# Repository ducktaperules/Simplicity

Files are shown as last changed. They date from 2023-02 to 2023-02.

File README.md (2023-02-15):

<h1 align="center">Simplicity</h3>

<p align="center"> A compact and easy to build printed printer
    <br> 
</p>

<p align="center">
  <a href="" rel="noopener">
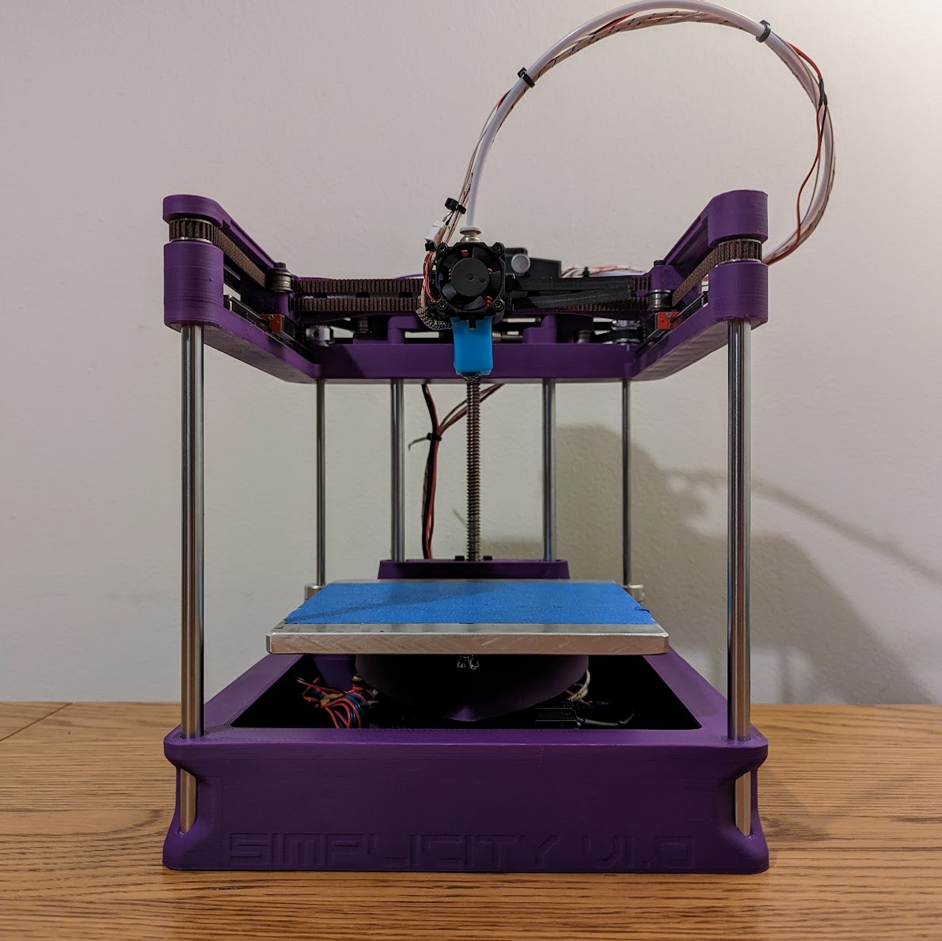
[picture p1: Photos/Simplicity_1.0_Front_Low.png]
Project logo
 </a>
</p>

  <br>

<!-- 
## 📝 Jump To Useful Things:
- [Quick Start](#get_started)
- [Info about Simplicity](#info)
- [Features](#features)
- [Inspiration](#inspiration)
- [Ethos](#ethos)
- [To Do List](#to_do_list)
- [Future Scope](#future_scope)
- [Authors](#authors)
- [Acknowledgments](#acknowledgments)
-->

## 👏 Quick Start
### - [BOM And CAD](/CAD/)
### - [Build Guide](/Instructions/)

  <br>

## 🧐 Info about Simplicity 
Simplicity was designed as a compact desktop printer for the everyman. Its well suited to printing small parts quickly and accurately. Its easy to source, build and maintain, whilst looking good enough that you can keep it on show and accessible at all times.

## 📱 Features 
 - CoreXY Design
 - 3D Printed Frame (prints on 220x220mm bed)
 - 120x120x100mm print volume (easy to extend Z as needed)
 - Voron V0 Bed Support
 - Looks Good
 - Few separate parts to print.
 - Less than 500g of filament to print all parts.
 - Integrated belt tension adjustment.
 - Bottom mounted motors for improved stability

<br>

## 💡 Inspiration 
### Voron V0 (https://github.com/VoronDesign/Voron-0)
The V0 is one of the most popular desktop printers that has shown what small format FDM printers are capable of. I wanted one for a long time however theres 3 main things that have put me off:
 -  Sourcing - There are so many the different parts to source. Aluminum extrusions, Odd size motors, Custom Beds, Specific extruders, acrylic panels, 
 - Printing - As of today the V0.2 print list currently has 143 parts to print. The thought of having to download, organize, slice, print and clean this many parts is a daunting task in its self. Especially if you don't already own a printer that tuned to perfection.
- Building - For some this is the fun bit, but for many this can be a tedious and frustrating endeavour. 

### Rolohaun Rook (https://github.com/rolohaun/Rook)
The Rook is a relatively new printer focused around making small format printers more accessible. I think the idea of using a printed frame is great and theres now enough of them out in the wild to prove that this can be a reliable option if designed well. I also love the use of vertical linear rods for both the bed and as structural frame component. 

That said, the Rook design optimized for function over aesthetics. IMO it also has an unnecessary number of individual parts to print that require a decent tolerance to work correctly. 

<br>

## 🤘 Ethos 

### Simple to Print
Simplicity is designed to have as few separate parts as possible, all of which should be printable without supports. Its also designed so that tolerances in most places are not critical and everything should fit together first try.

### Built from common parts
Due to the small lightweight design, good results can easily be achieved with cheap components or old spare parts. Any Junker 42mm stepper motors will give speeds and accelerations. Im also using the Creality hot end as they are available everywhere and many even have them spare from previous printers.

### Easy to mod
The stock configuration i have provided is the minimum needed to get up and running however i expect there will be many mods allowing better cooling, different print heads, enclosures, and electronics mounting for many different control boards. 
<br>The full .STEP file is now available for modding in the CAD folder.

<br>

## 📋 To Do List 
There are a few things i need to do in the short term.
 - Upload STL files ✅
 - Upload STEP files
 - Add pictures ✅
 - Add instruction manual ✅
 - Write BOM ✅(kinda)
 - SORT OUT LICENSE
 - Design parts variant that use M3 heat set inserts rather than self tapping screws.
 - Maybe Belted Z Mod

<br>

## 🚀 Future Scope 
There are a lot of things i would like to improve in the future.
 - Printhead with built in part cooling fans 
 - Electronics Cover for those who want to  hide their shame
 - Full enclosure with door and lid for better printing of ABS

<br>

## ✍️ Authors 
- [@ducktaperules](https://github.com/ducktaperules) - Idea & Initial work

<br>

## 🎉 Acknowledgments 
- [@rolohaun](https://github.com/rolohaun) - Thanks for the inspiration and for hosting a great community on discord who provide constant motivation.

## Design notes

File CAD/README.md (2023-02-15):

<p align="center">
  <a href="" rel="noopener">
 
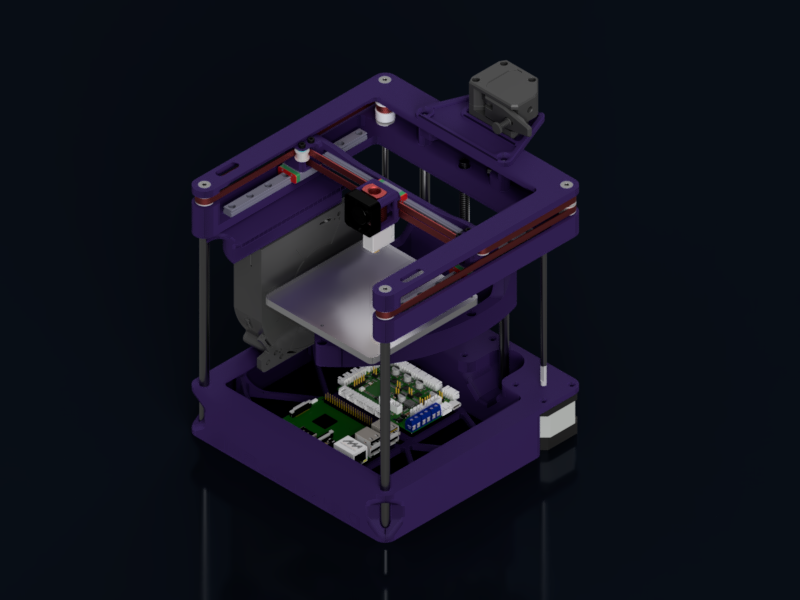
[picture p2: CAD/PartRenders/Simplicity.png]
</a>
</p>

<h1 align="center">Parts List</h1>

## BOM

Big Parts:
 - Control Board - I recommend SKR Pico with raspberry pi and klipper, but you can use whatever printer board you have access to.
 - 3x NEMA 17 stepper motors less than 40mm in length (For XYZ axis).
 - Extruder and Stepper - Any you have available. The stock Creality will fit but i recommend a dual gear like the bondtech BMG clones available from ali-express or amazon.
 - Hot End - Again, creality ender/CR10 hot end is fine but i recommend a high flow nozzle. im using a cheep volcano block and nozzle from amazon.
 - Bed - 120x120mm beds compatible with Voron V0 or Rook should fit. Otherwise Im using a diy bed made from a 150x150mm scrap of aluminum with V0 compatible mounting. If not using a printed bed i have seen some Rook's with printed beds. 
 - Power supply - whatever you can find 24V PSU is ideal but im just using a 20V 6.5A Dell laptop supply, its a little less powerfull but much easier to mount externally.
 - 3010 fan for hot end.
 - Optional 120mm radial blower for part cooling.

Bearings & Drive:
 - 3x 150mm MGN9 rails with MGN9C carriages
 - 4x 8mm smooth rods 200mm length.
 - 2x LM8UU Long 45mm bearings (dual short bearings might work instead but not tested)
 - 1x 8mm lead screw and nut, ~150mm length
 - 20x F695 Bearings (5x13x4 flanged). Usually available in sets of 10.
 - 8x F623 Bearings (3x10x4 flanged). Usually available in sets of 10.
 - 2x 20T GT2 pulleys.
 - 2m of Gates GT2 Belt
 - 2x 5mm to 5mm motor couplers
 - 1x 5mm to 8mm motor coupler 
 - 2x 160mm 5mm rod (steel, aluminum, carbon, shouldn't matter what)

Hardware: 
 - 24 M2.5 x 8mm self tapping screws (i used Torx T10, will try find a good link ASAP)
 - 6 M2.5 x 16mm self tapping screws (i used Torx T10, will try find a good link ASAP)
 - 6x M5x30 CSK
 - 2x M5x25 CSK (+4 if using my electronics tray)
 - 2x M5x25 Cap Head (tension adjusters so cap or dome works too)
 - 8x M5 Heatset Inserts (7mm diameter by <8mm deep ),(+4 if using my electronics tray)
 - 20x M5 Washer (should be 1mm thick)
 - 8x M3 Washer (should be 0.5mm thick)
 - 8x M3x25 Cap Head (or dome head if your a sadist)
 - 4x M3x6 Cap Head (see above)
 - 12x M3x8 CSK (for stepper motors)

---

## Printed Partrs

I have been printing all parts in ABS+ as i plan to print PETG in the future, but if you only plan to print PLA i would expect a PLA frame to be fine.

I sliced with 0.2mm layers, 15% infill, 3 perimiters and 4/5 bottom/top layers.

Total filament used was around 430g and total print time was around 24 hours on my ender 5 plus with conservative speed settings.

### Frame Base
The base is the largest part. it should print top side down.
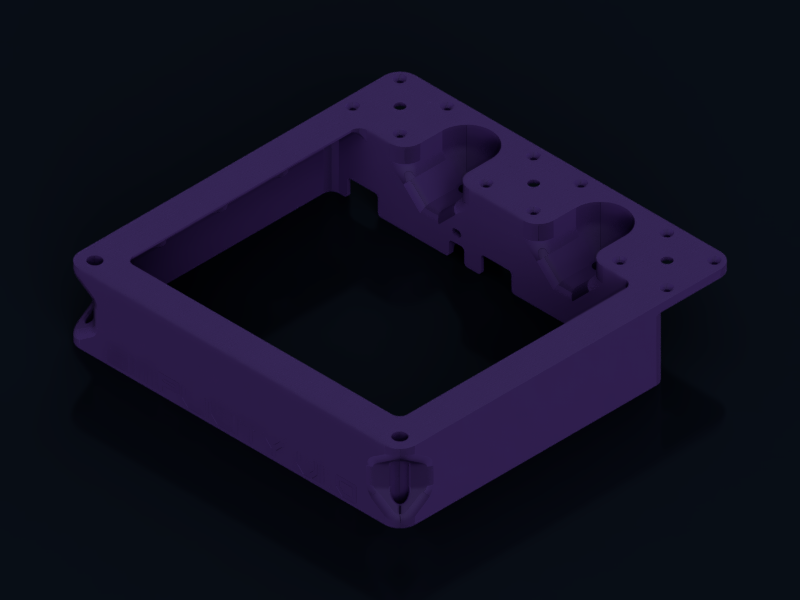
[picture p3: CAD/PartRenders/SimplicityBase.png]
<p></a></p>

### Frame Mid and Frame Top
These 2 parts bolt together to form the main top assembly.
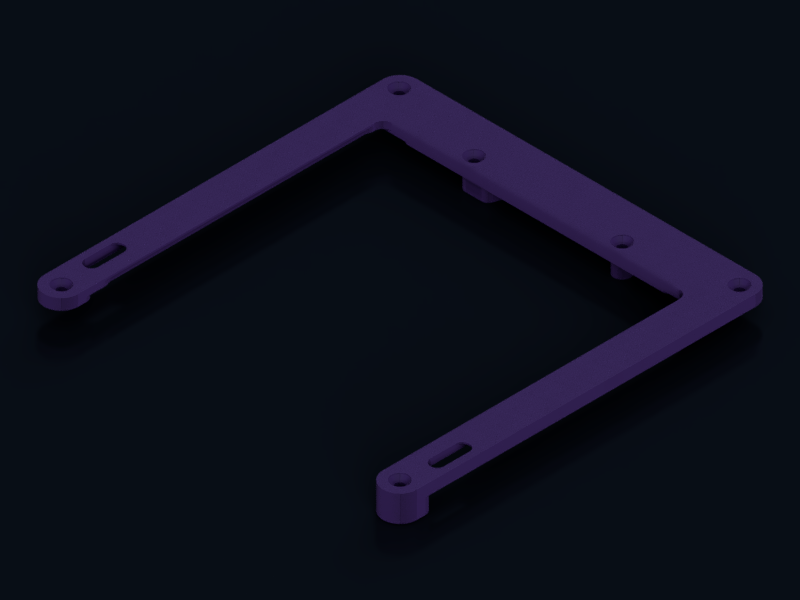
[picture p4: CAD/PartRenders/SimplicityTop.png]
<p></a>
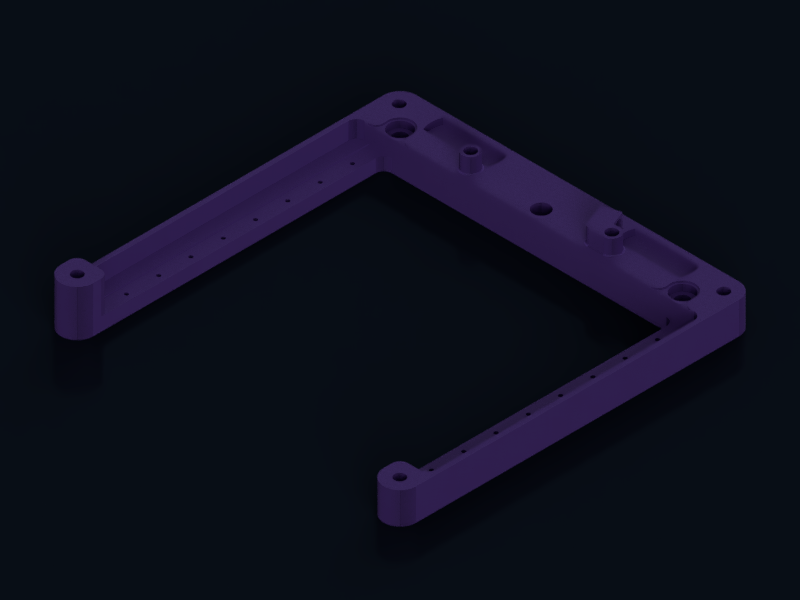
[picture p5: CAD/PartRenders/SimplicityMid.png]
</a></p>

### Tensioner (x2)
You need 2 of these. They hold the adjustable belt pulleys to tension the belt. They should sit flat on the bed with the widest part of the slope at the bottom. 
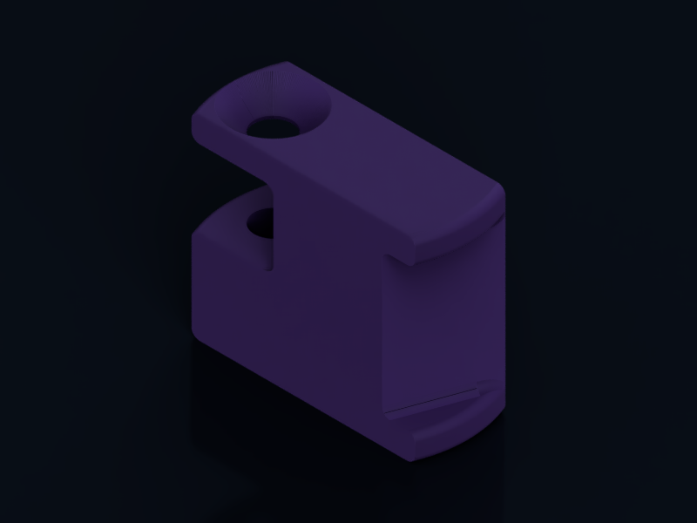
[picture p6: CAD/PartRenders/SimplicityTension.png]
<p></a></p>

### X Gantry
Printed on its back with the rail surface on the top.
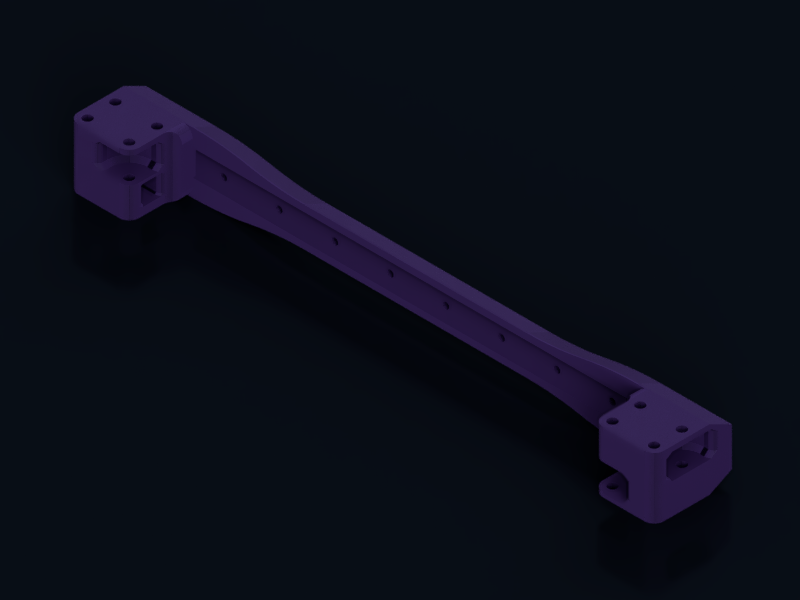
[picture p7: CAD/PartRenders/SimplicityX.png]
<p></a></p>

### Print Head
Printed on its back.
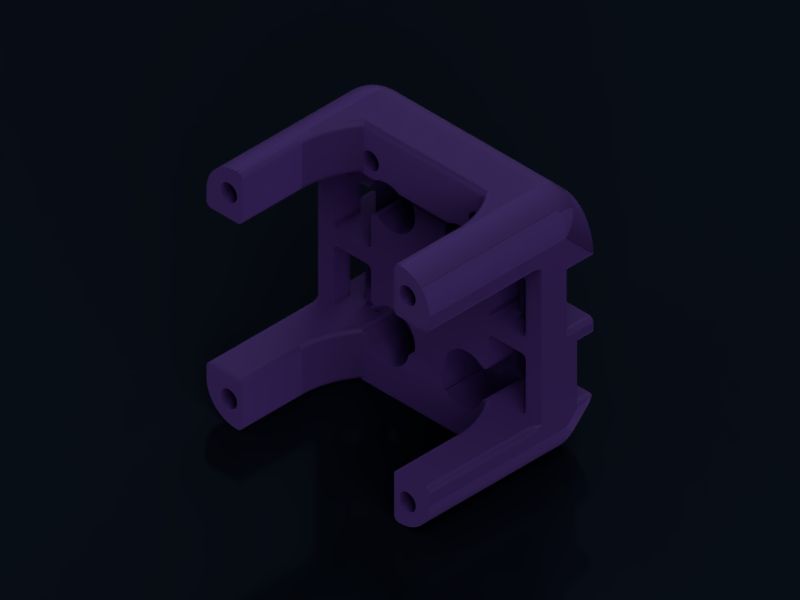
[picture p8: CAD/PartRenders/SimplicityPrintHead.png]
<p></a></p>

### Bed
Printed with the large flat side down, a small amount of support is usually needed for the overhand near the nut for the threaded rod
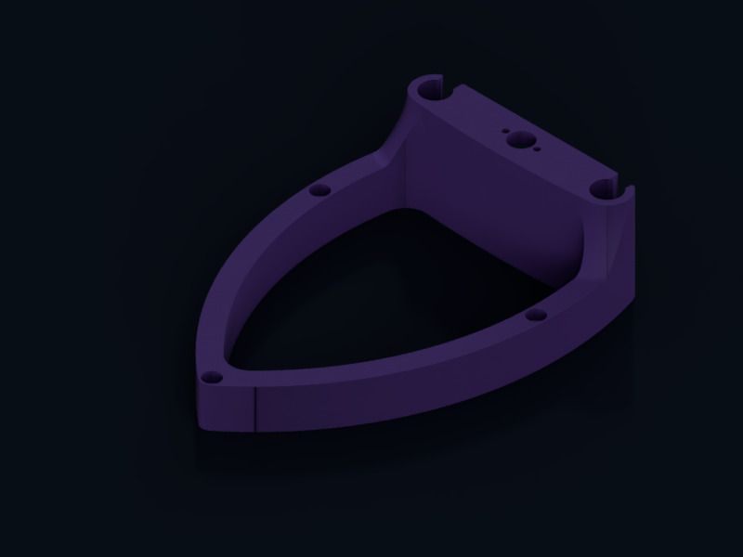
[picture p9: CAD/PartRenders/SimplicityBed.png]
<p></a></p>

### Extruder mount
Optional part that will alow for easy mounting of most extruders that use a standard stepper motor. I have used both the original Creality extruder as well as the bondtech Clone shown in my photos.
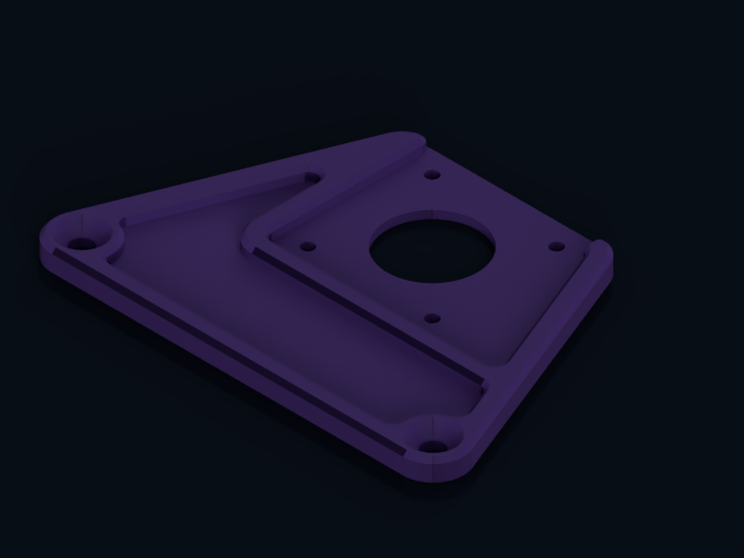
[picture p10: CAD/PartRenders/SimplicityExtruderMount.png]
<p></a></p>

### Electronics mount
Optional part that will alow for easy mounting of raspberry Pi and SKR Pico driver board. if your using something else this part can be modified to support different control boards.
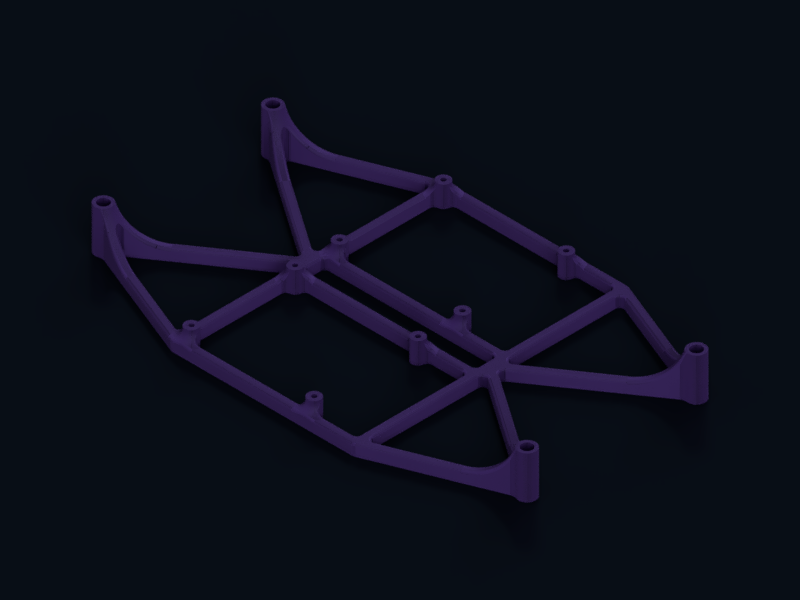
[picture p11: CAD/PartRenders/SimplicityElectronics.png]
<p></a></p>

### Cooling
This is a quick bodge to add an RCS style part cooling fan. its not optimized but it will get you going. it takes a 120mm blower fan. It fits mine, I dont know if they are all the same or not.
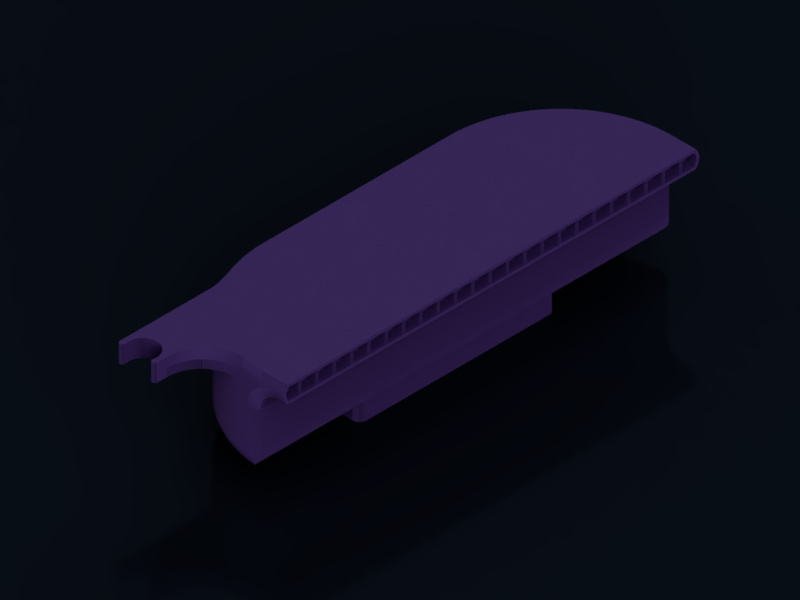
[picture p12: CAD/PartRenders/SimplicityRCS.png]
<p></a>
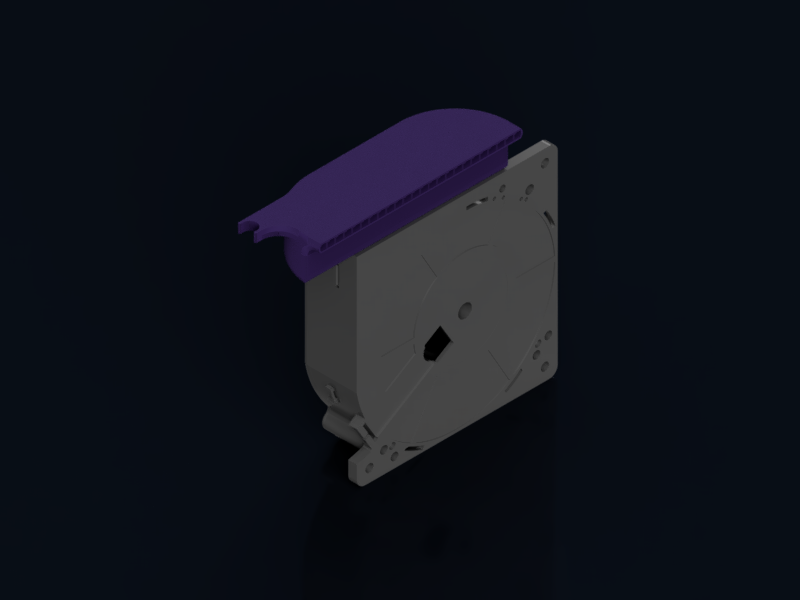
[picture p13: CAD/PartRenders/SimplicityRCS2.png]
</a></p>

### Draft Shield (Guard)
CURRENTLY UNTESTED - This is a simple print that can be printed in vase mode and is designed to provide a semi inclosed bed, offering a little protection from drafts. Its not compatible with the cooling fan above
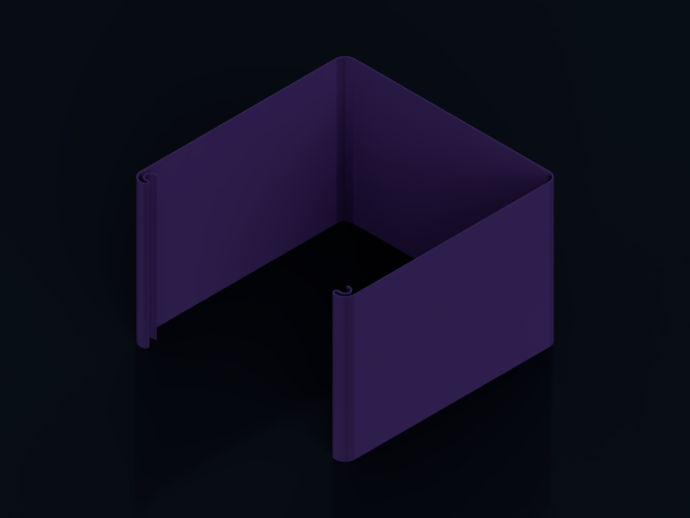
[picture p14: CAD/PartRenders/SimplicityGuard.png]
<p></a></p>

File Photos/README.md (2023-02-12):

<h1 align="center">Gallery</h1>

</a>
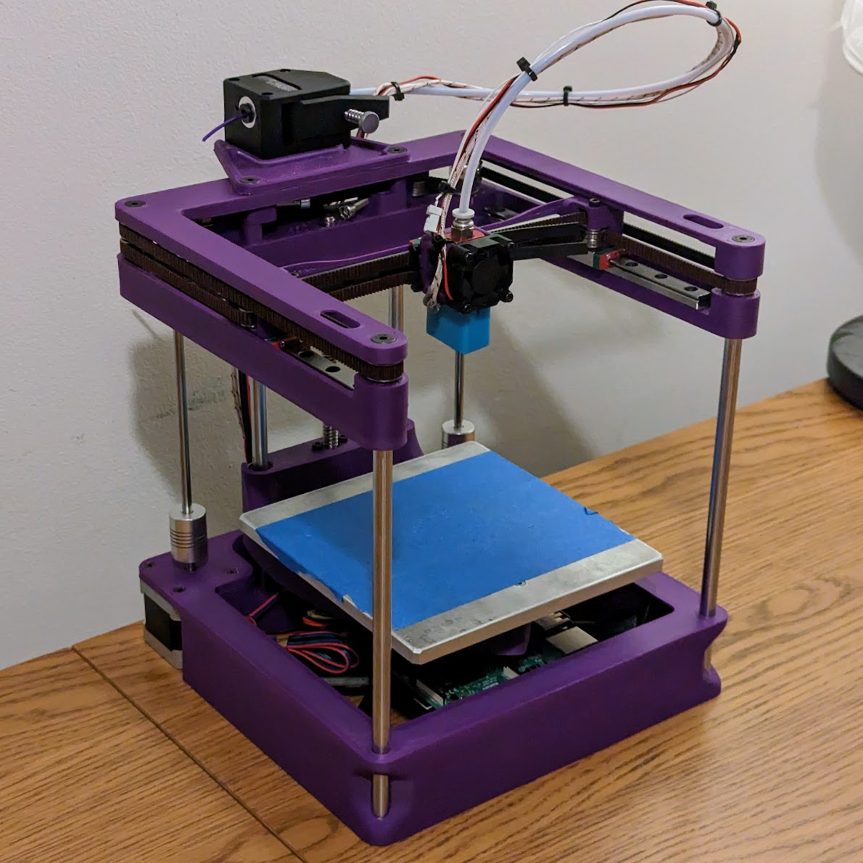
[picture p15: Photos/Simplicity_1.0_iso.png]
</a>
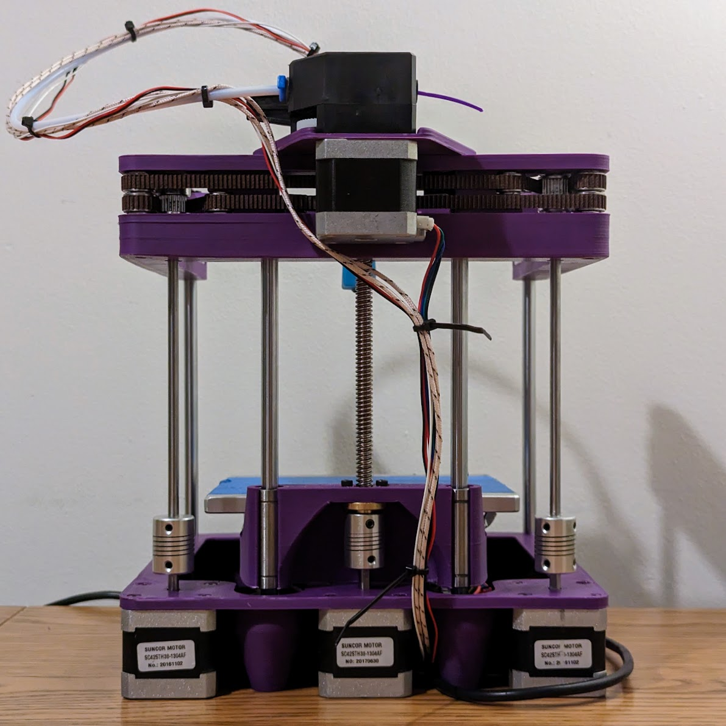
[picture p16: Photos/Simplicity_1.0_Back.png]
</a>
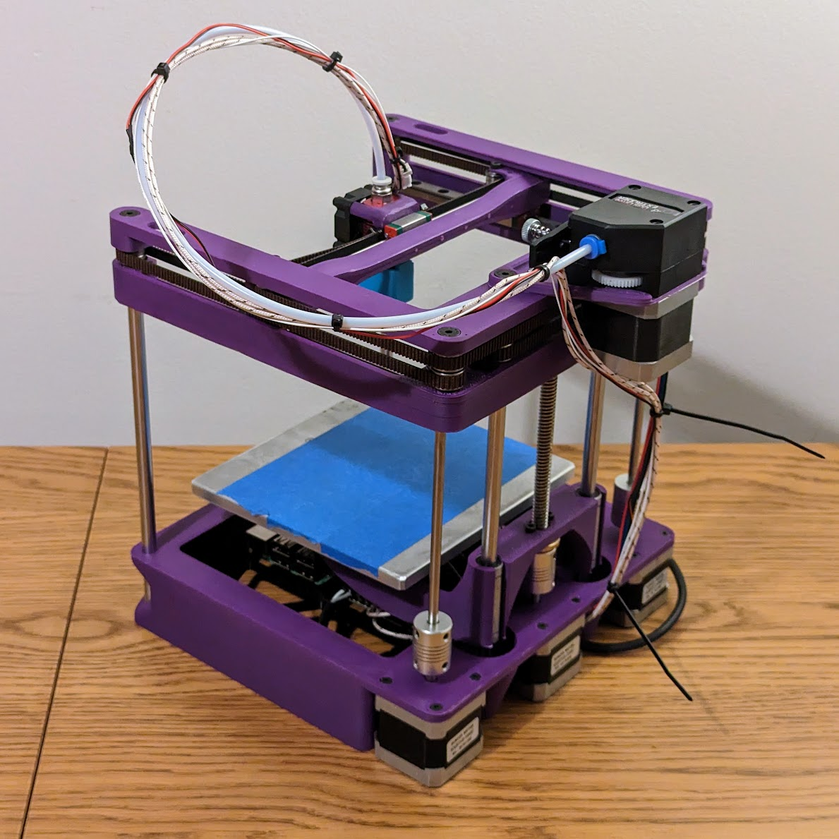
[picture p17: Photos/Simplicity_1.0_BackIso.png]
</a>
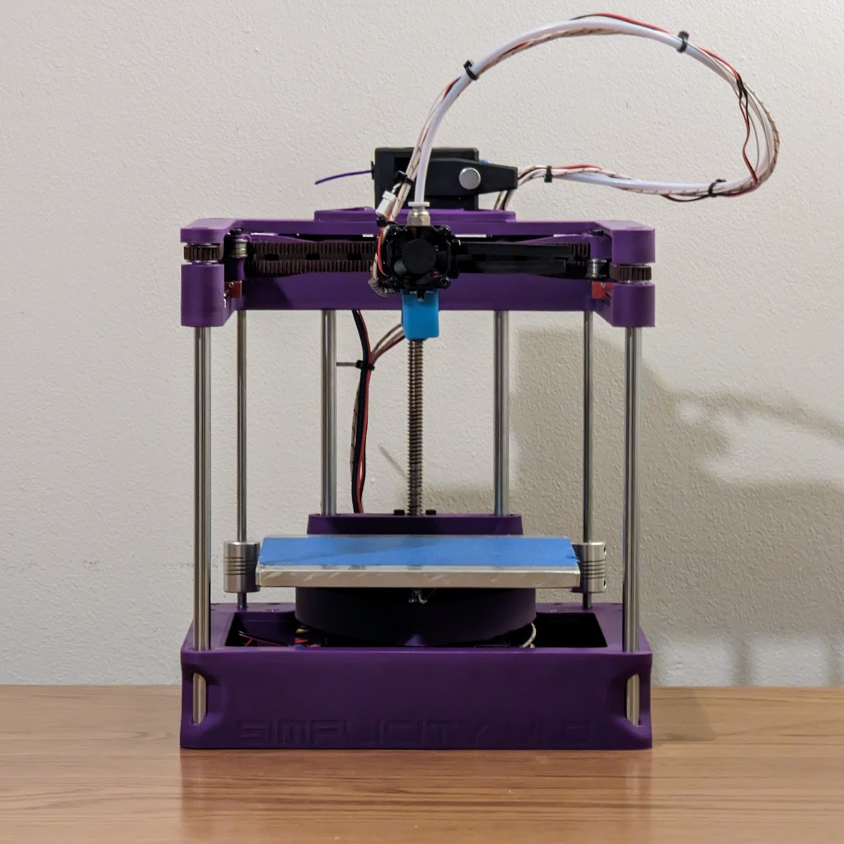
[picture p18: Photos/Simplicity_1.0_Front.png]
</a>

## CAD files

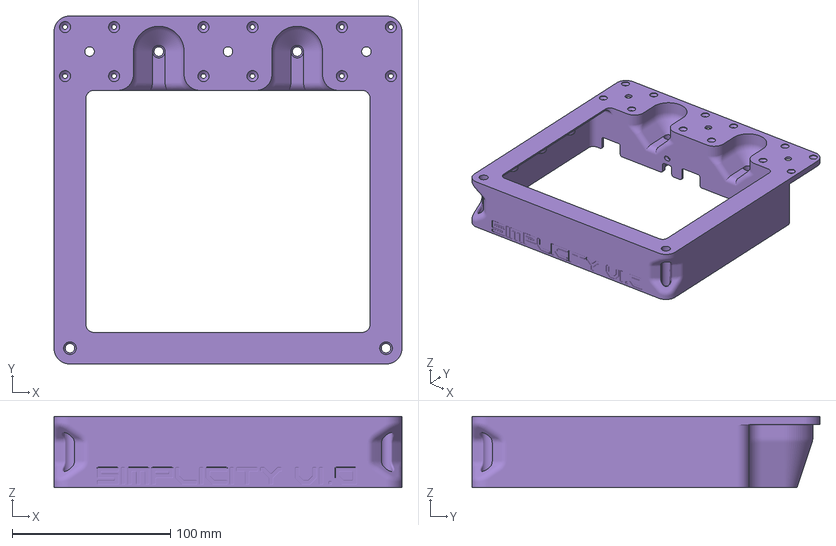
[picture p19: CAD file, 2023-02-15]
CAD/PartFiles/SimplicityBase.3mf
220.0 x 220.0 x 45.0 mm

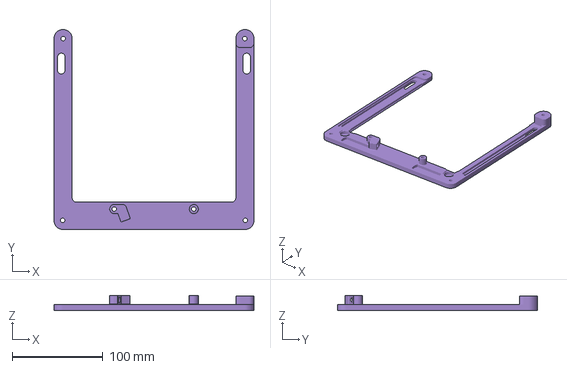
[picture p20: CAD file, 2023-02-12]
CAD/PartFiles/SimplicityTop.3mf
220.0 x 220.0 x 16.0 mm

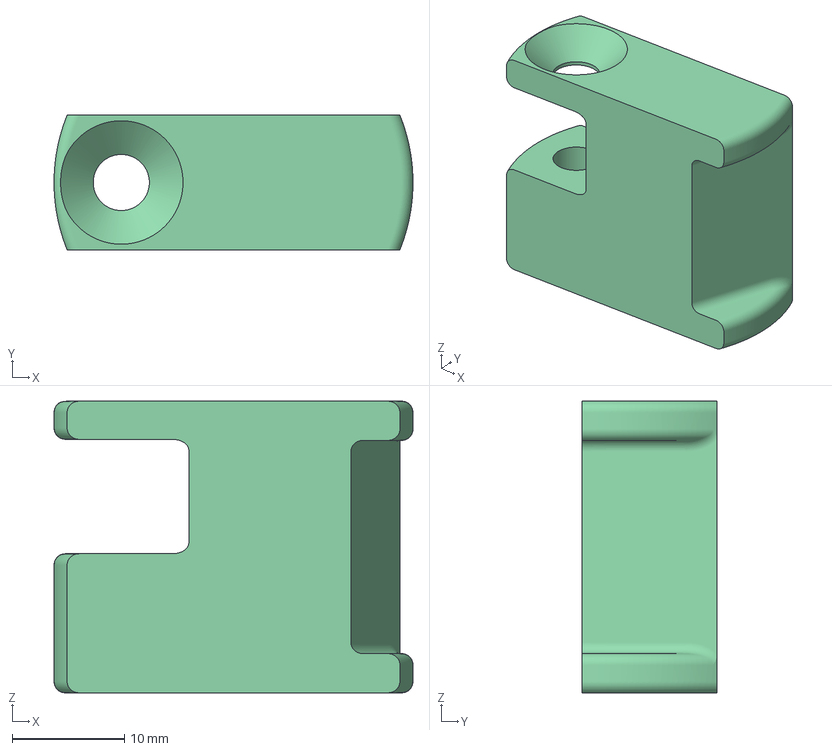
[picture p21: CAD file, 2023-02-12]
CAD/PartFiles/SimplicityTension.3mf
32.0 x 12.0 x 26.0 mm

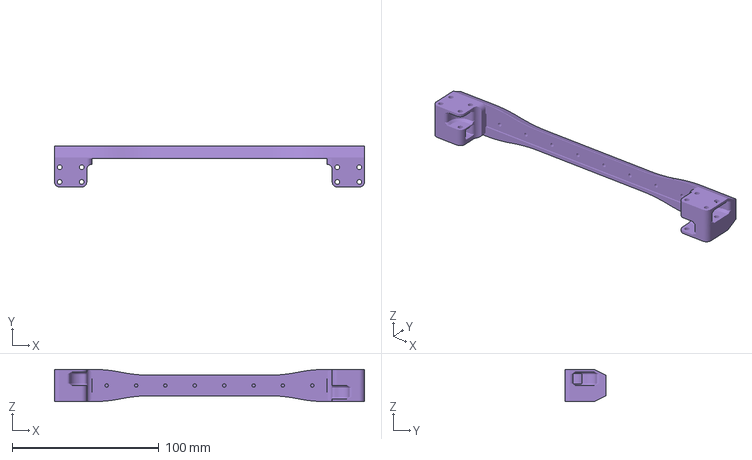
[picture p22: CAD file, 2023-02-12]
CAD/PartFiles/SimplicityX.3mf
211.0 x 28.0 x 22.0 mm

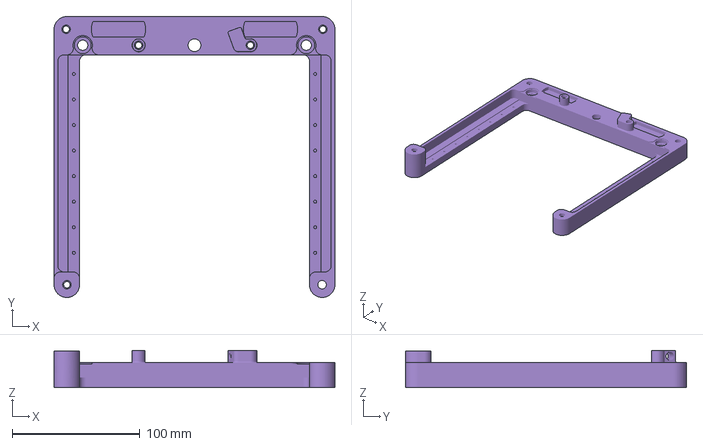
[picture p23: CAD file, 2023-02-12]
CAD/PartFiles/SimplicityMid.3mf
220.0 x 220.0 x 29.0 mm

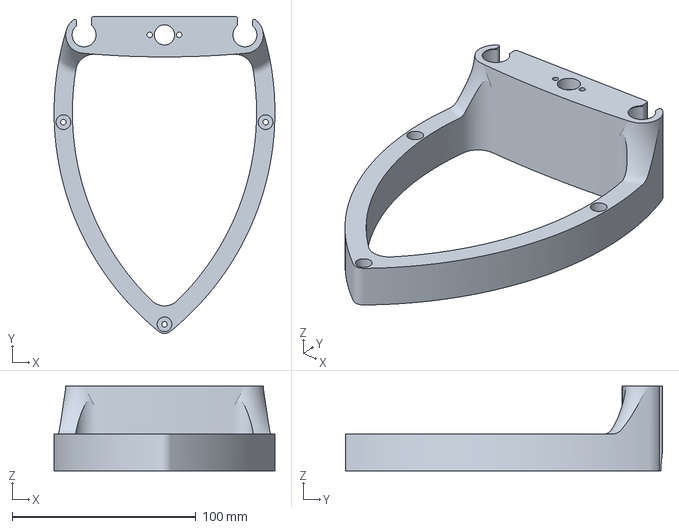
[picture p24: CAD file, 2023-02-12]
CAD/PartFiles/SimplicityBed.3mf
120.2 x 172.5 x 46.0 mm

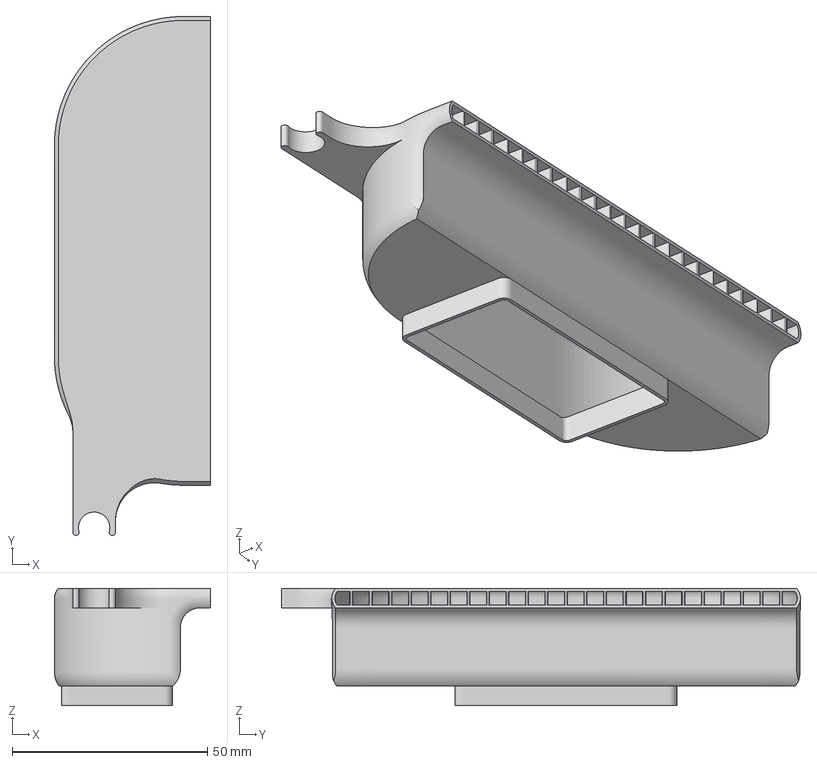
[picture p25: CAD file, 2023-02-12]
CAD/PartFiles/SimplicityRCS.3mf
40.0 x 132.8 x 30.0 mm

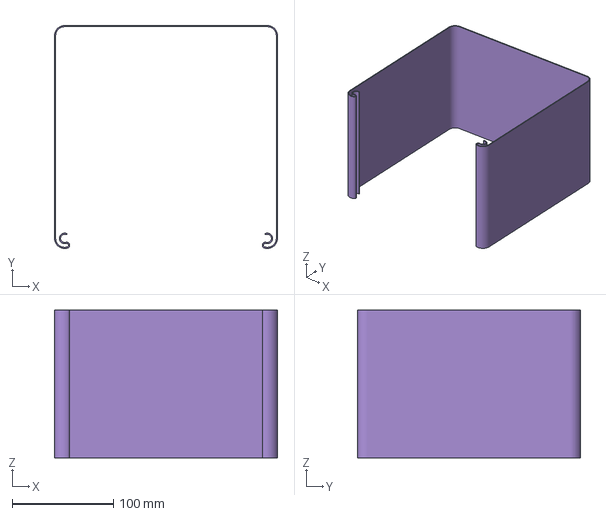
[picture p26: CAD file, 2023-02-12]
CAD/PartFiles/SimplicityGuard.3mf
220.0 x 220.0 x 146.0 mm

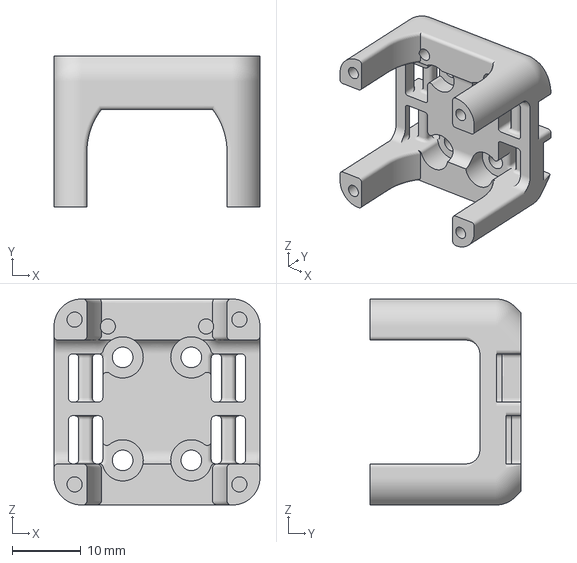
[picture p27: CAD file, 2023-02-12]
CAD/PartFiles/SimplicityPrintHead.3mf
30.0 x 22.0 x 30.0 mm

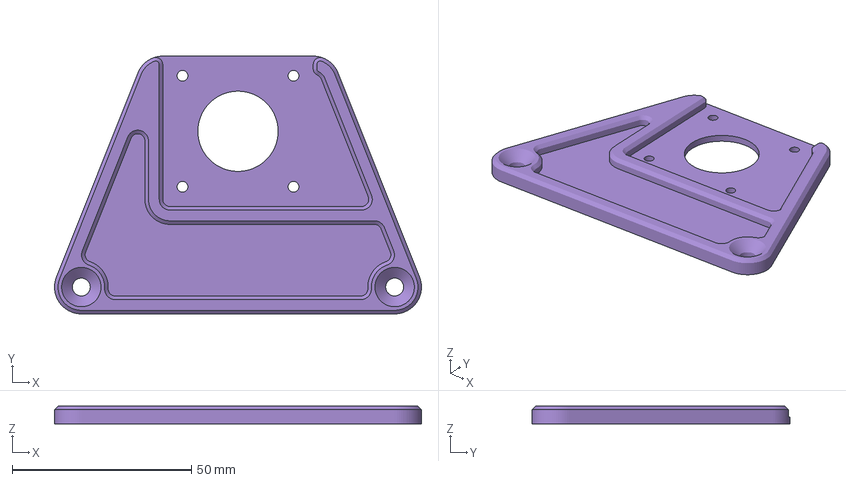
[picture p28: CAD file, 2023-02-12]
CAD/PartFiles/SimplicityExtruderMount.3mf
102.5 x 72.0 x 5.00 mm

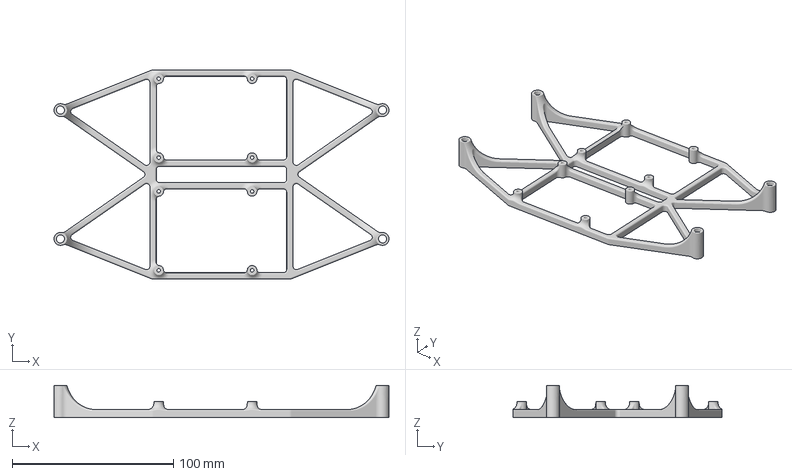
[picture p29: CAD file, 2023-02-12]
CAD/PartFiles/SimplicityElectronics.3mf
208.0 x 130.0 x 20.0 mm

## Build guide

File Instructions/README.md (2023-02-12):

<h1 align="center">Build Guide</h1>

## Step 1 - print and prep your parts

Print all nessacary parts from the part list found in the [parts list here](/CAD/)
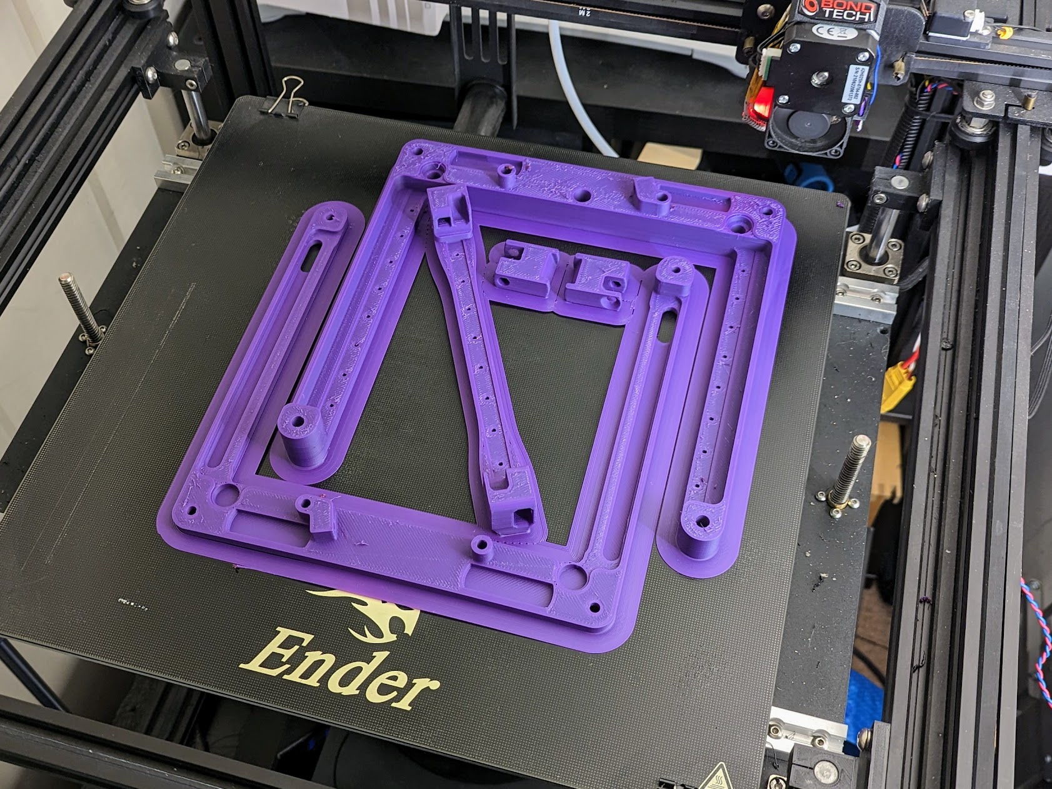
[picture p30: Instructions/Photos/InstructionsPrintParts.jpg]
<p></a></p>

Remove any brims and support. deburr any sharp edegs and remove any bumps on surfaces.
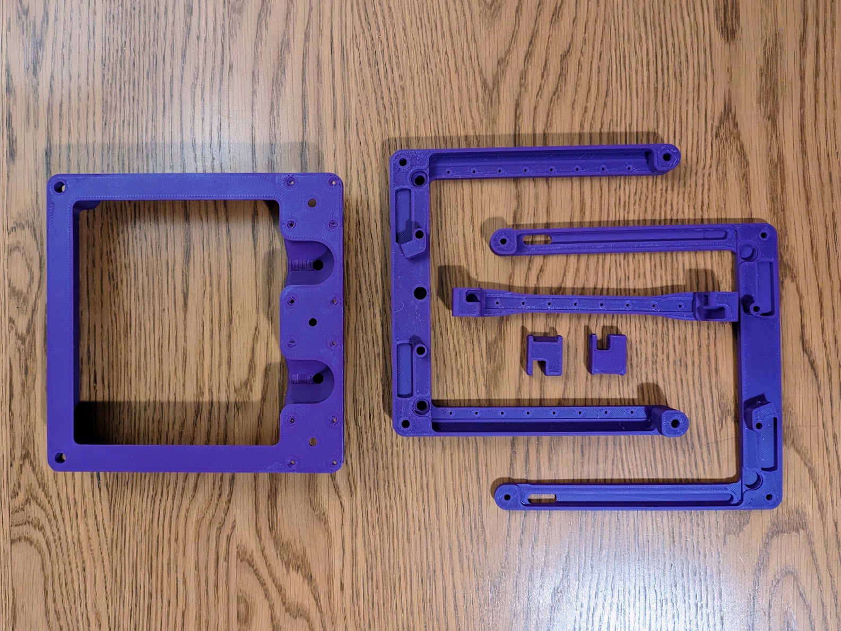
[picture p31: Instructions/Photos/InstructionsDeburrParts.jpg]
<p></a></p>

I recommend to clearance drill most holes to the correct size to ensure easy assembly.

drill 3mm for the 8 holes in the X stage, the 12 stepper motor screws in the base part, the 4 in the Print Head, and the 5 in the bed mount.
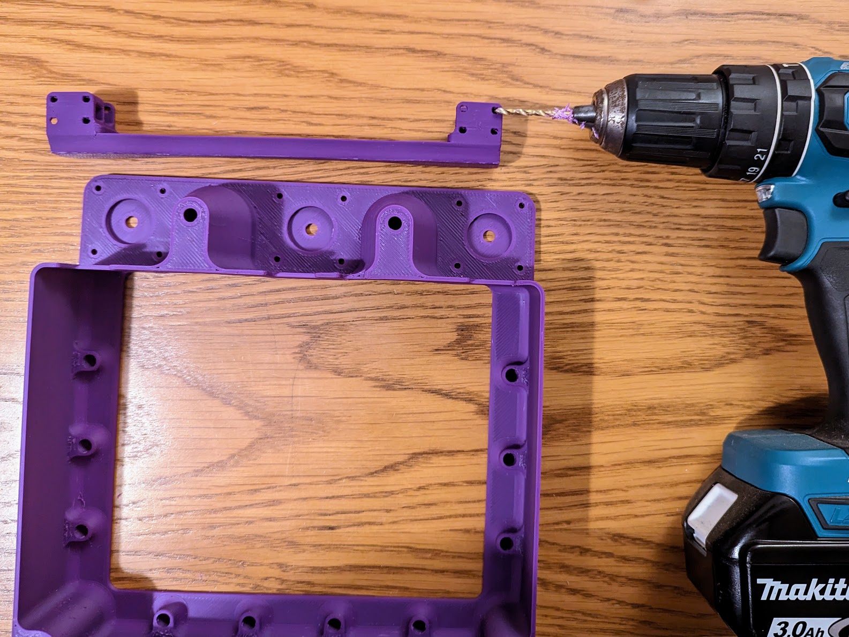
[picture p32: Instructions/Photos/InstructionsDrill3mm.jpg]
<p></a></p>

drill 5mm for the 7 holes in both the mid and top parts (dont forget the sideways one for the tensioner), as well as the holes through the tensioners and the 2 in the extruder mount if your using it.
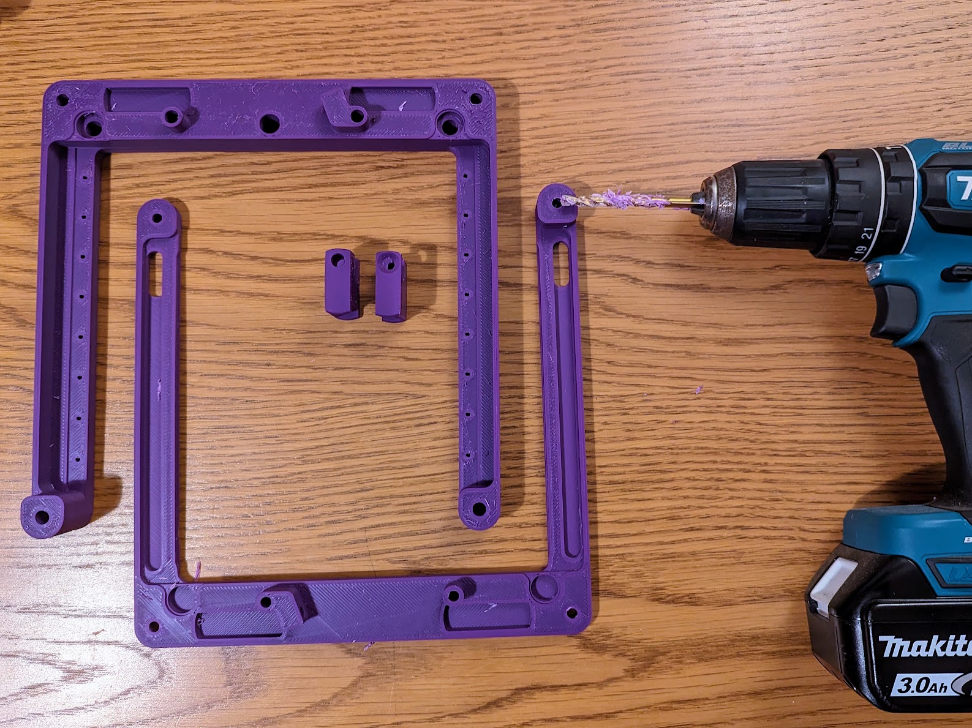
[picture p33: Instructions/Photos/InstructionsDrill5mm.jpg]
<p></a></p>

drill 8mm for the 2 holes in both the base and mid parts.

IMPORTANT NOTE: These 8mm holes do not go all the way through so drill carefully till you touch the step. On the base this is most the way through, on the mid part its about 15mm in.
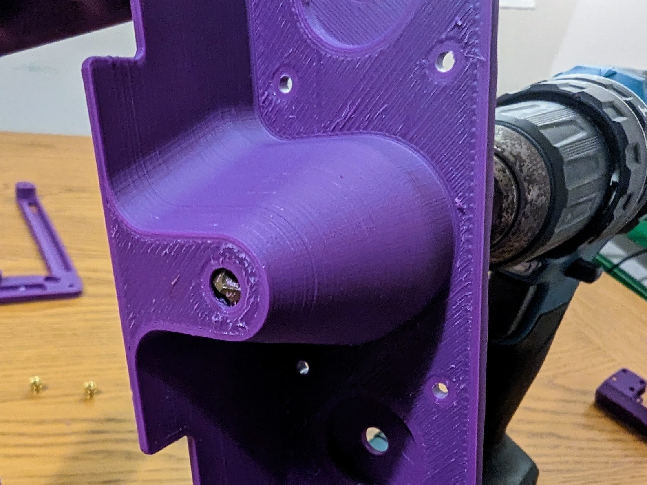
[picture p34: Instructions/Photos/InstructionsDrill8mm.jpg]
<p></a>
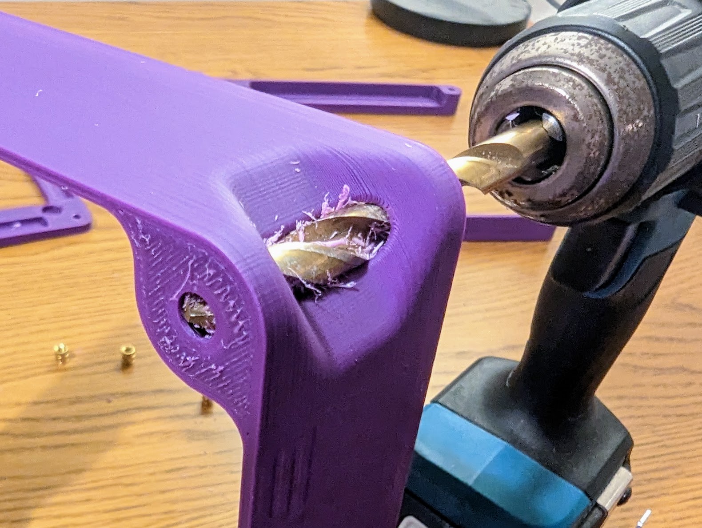
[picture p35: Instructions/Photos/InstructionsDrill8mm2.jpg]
</a></p>

Finally put the M5 heat set inserts in. There are 7 in the mid part, 1 in the top and 1 in each tensioner.
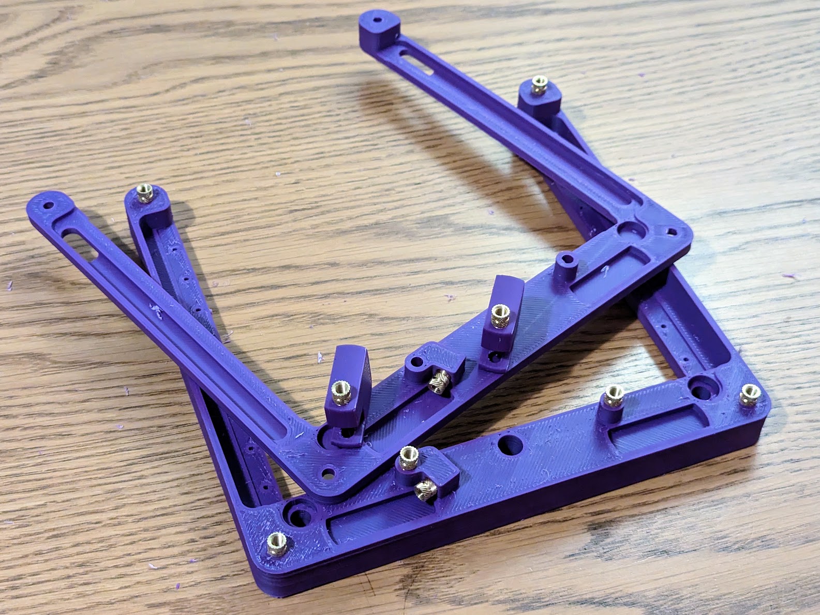
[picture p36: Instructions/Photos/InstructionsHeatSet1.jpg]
<p></a>
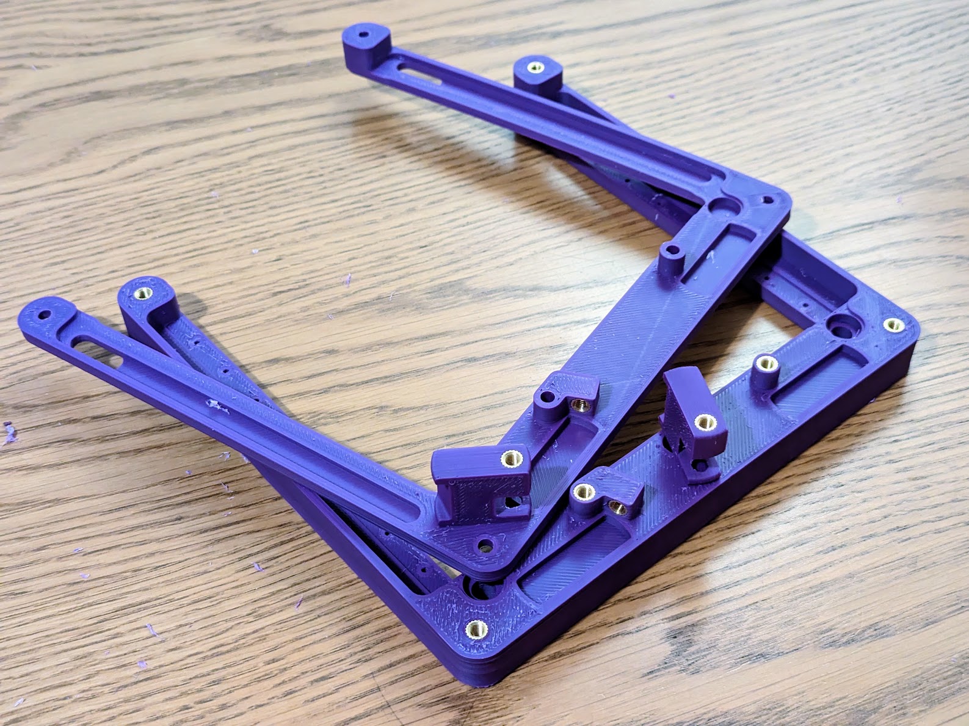
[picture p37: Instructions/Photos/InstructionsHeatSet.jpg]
</a></p>

---

## Step 2 - Build The Base

The 8mm Steel rods can be inserted into the 4 holes in the base. they must be pushed down until they bottom out on the lip at the bottom of the print
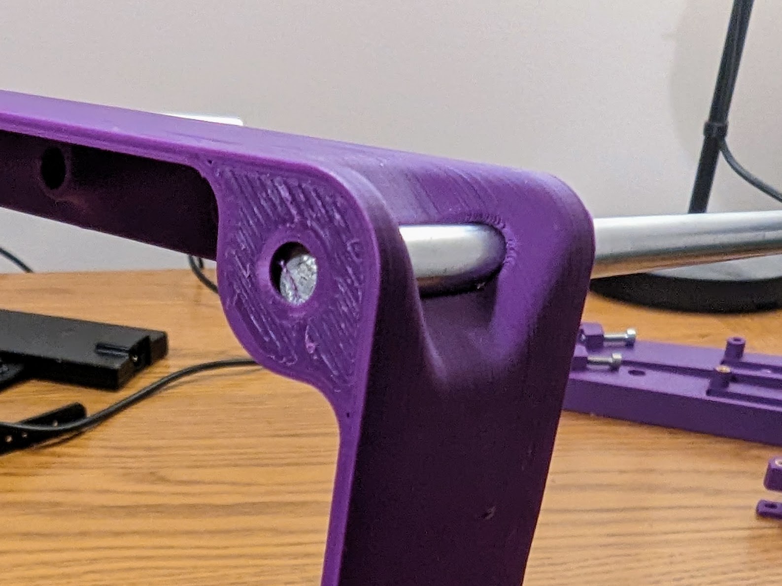
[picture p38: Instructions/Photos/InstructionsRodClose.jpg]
<p></a></p>

Next the 3 drive steppers can be mounted at the back with 12x M3x8 CSK screws. their cables or plugs should face inwards towards the electronics.
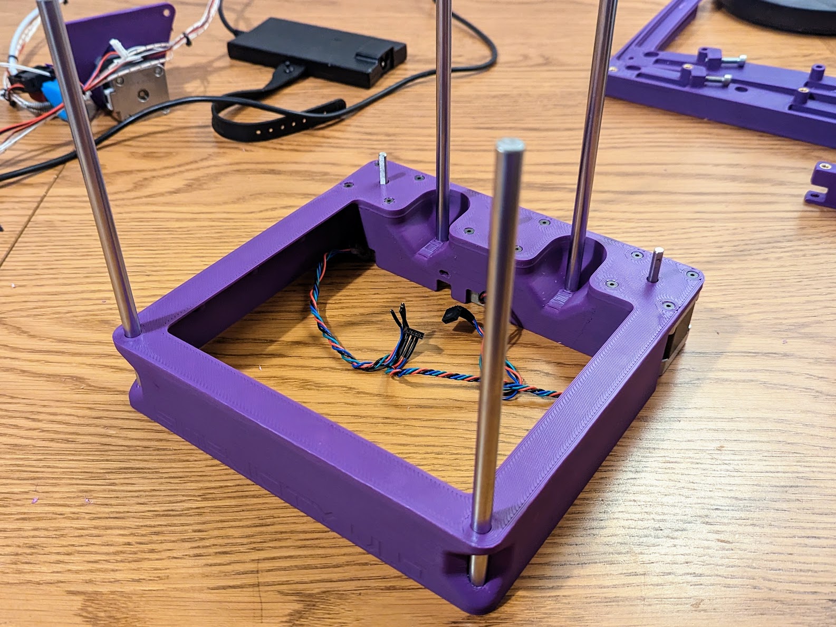
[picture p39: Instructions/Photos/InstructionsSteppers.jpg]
<p></a></p>

## Step 3 - Build The Bed

i forgot to take many pics of this but basically . . .

The bearings can be inserted into the bed.
The lead screw nut gets screwed in with 2x M3x8 screws. 
The lead screw can be inserted. 
The bed can be fitted.

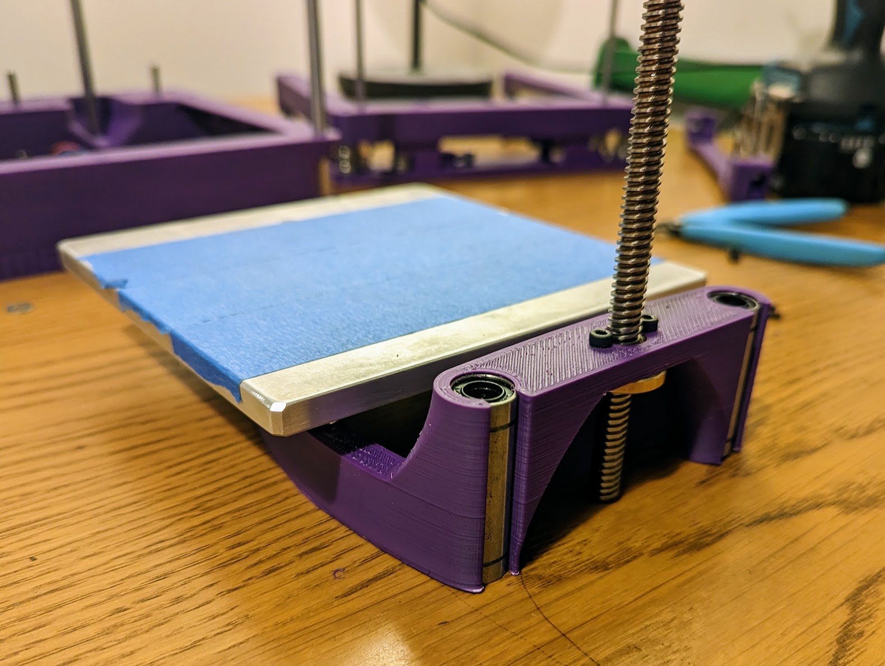
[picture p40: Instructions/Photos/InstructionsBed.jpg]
<p></a></p>

Once you lubricate the bearings, the bed can slide onto the rear linear rods.

The couplers can also be put in place but don't tighten them fully just yet.

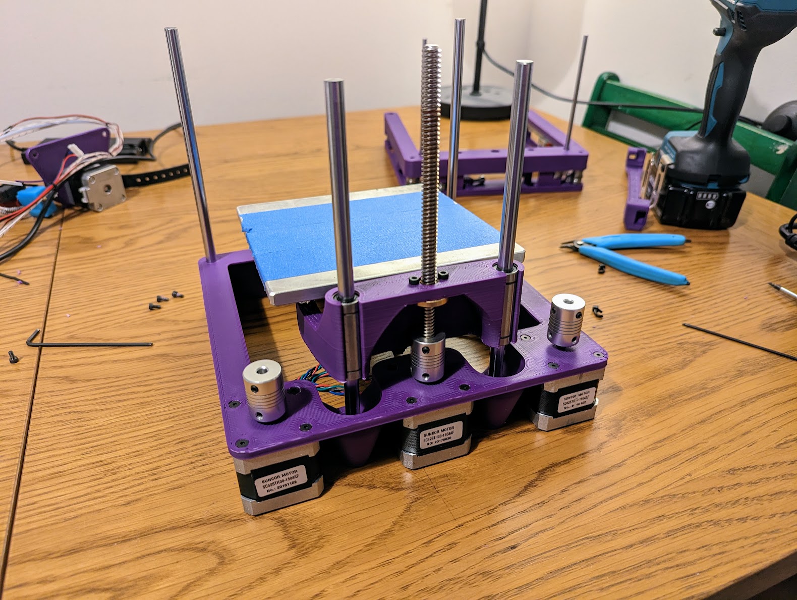
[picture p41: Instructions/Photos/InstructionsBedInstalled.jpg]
<p></a></p>

---

## Step 4 - Build The XY stage

This step is the most complex bit. mak sure to pay attention to how many washers are needed and where they go.

Firstly assemble the Tensionsers. These have M5x25 CSK screw inserted from one side then a stack of washer-bearing-bearing-washer before screwing into the heat set insert.

PROTIP: if theres extra plastic in the hole from putting in the heat set then it can be useful to first put the screw through from the heat set side to clear the hole, then remove it and reinstall the correct way.

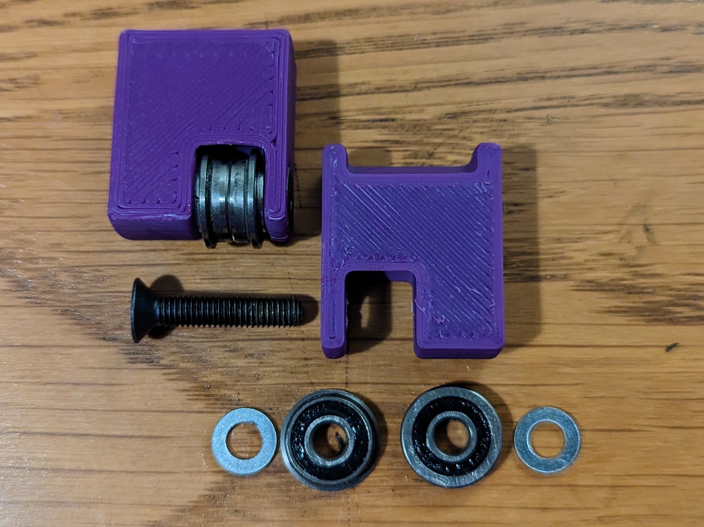
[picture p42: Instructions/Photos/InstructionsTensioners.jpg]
<p></a></p>

Next prepare the Drive Pulleys bars. On one end of the 5mm Rods you need to put a bearing,some washers and the pulley. The left and right assembly's are a little different so pay attention to the washer positions and pulley orientations shown below. There should be a single washer on the tooth side of the pulley and 2 washers on the grub side. The pulleys can be secured wit the grub screws and should have about 4mm of rod left sticking.

PROTIP: If the bearing is stiff to go on it can sometimes help to sand the rod a little by putting it in a drill and holding some mid grit sandpaper on the end.

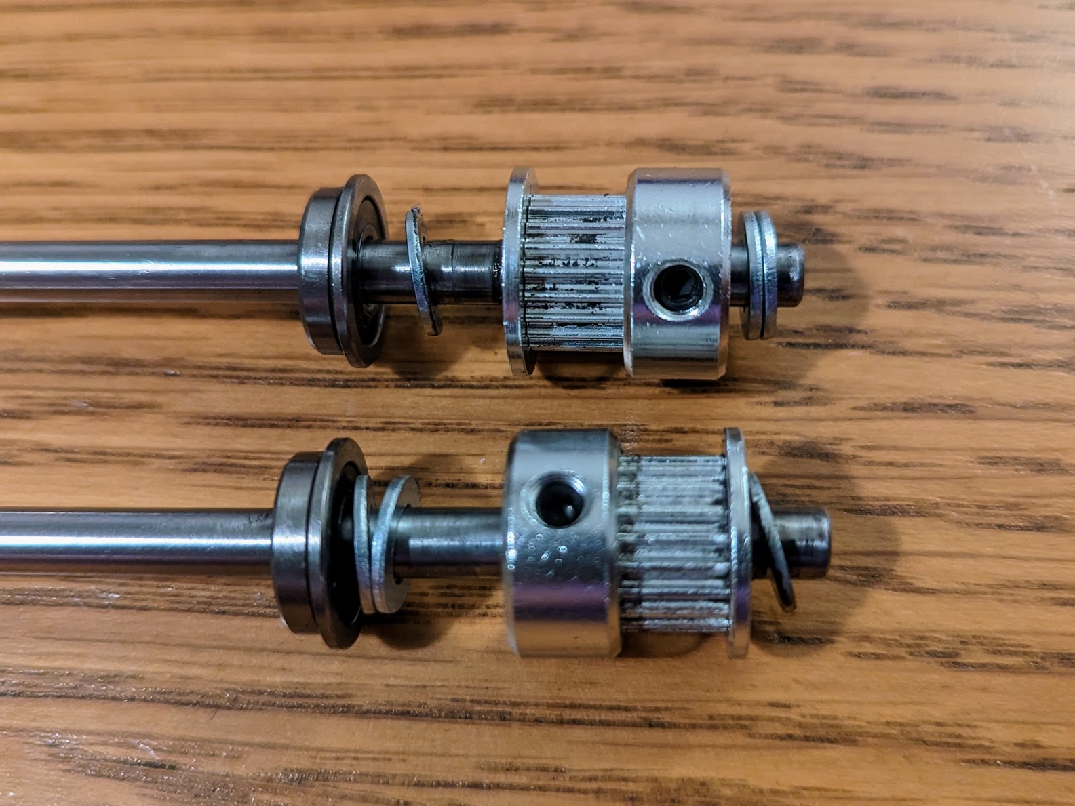
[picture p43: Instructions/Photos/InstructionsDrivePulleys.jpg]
<p></a></p>

Now is a good time to grease your rails.

Then the X rail can be secured to the Gantry with 8 screws, I recommend tightening screws from the middle outwards.

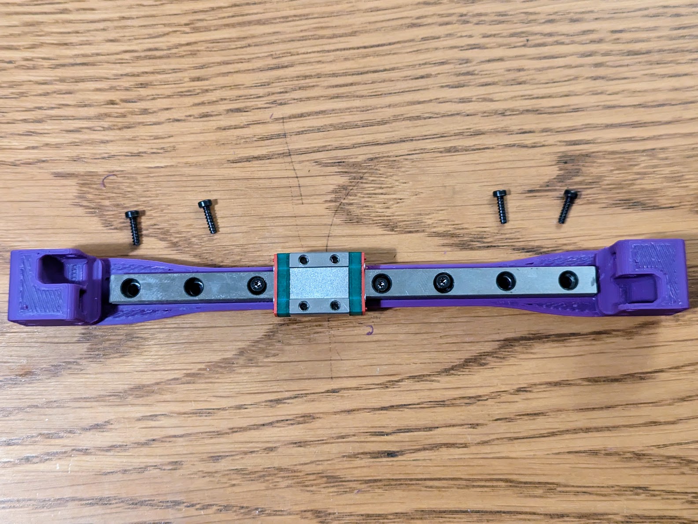
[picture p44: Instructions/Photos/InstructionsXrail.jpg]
<p></a></p>

The small bearings can then be put into the Gantry and the M3x25 screws inserted to hold them in place. Like with the tensioners these stacks should have washer-bearing-bearing-washer however this time using M3 washers and bearings.

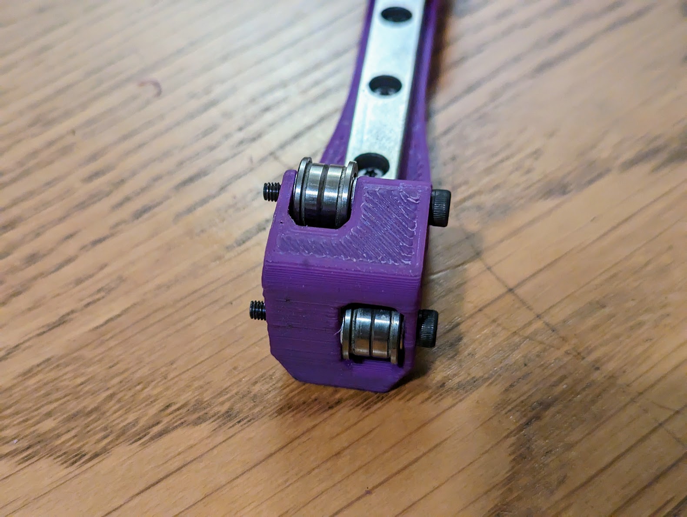
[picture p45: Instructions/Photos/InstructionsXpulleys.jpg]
<p></a></p>

The other 2 rails can then be placed on the Mid Section. at this pint you  want to just put the end 2 screws in loosely so that the rails can move around a little.

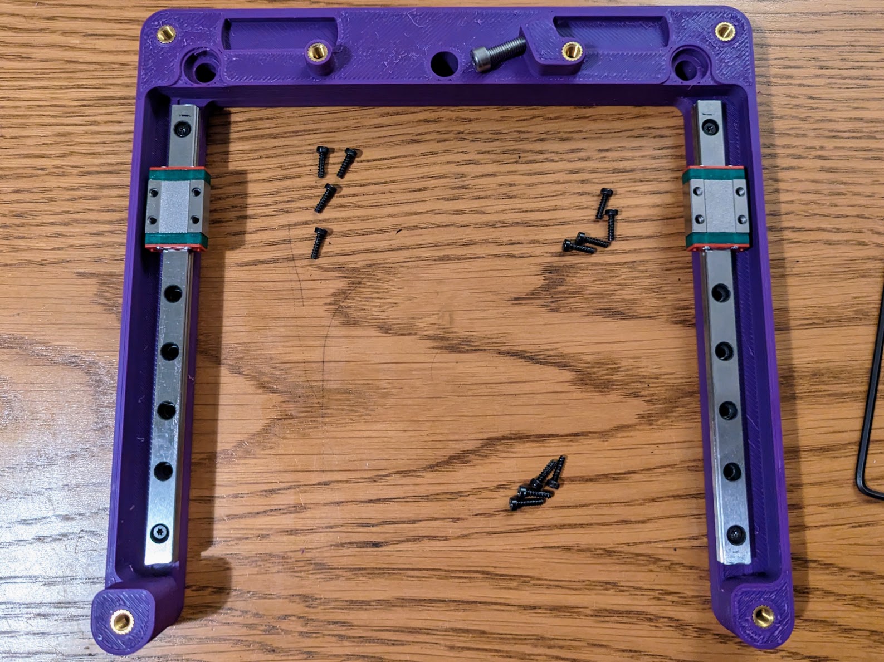
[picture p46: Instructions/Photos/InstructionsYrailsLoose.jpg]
<p></a></p>

The X gantry can now be placed on the Y bearing blocks and the screws inserted loosley. Both Y blocks should be pushed all the way to the back an then the gantry pulley screws can be tightened. This ensures that the gantry is mounted square.

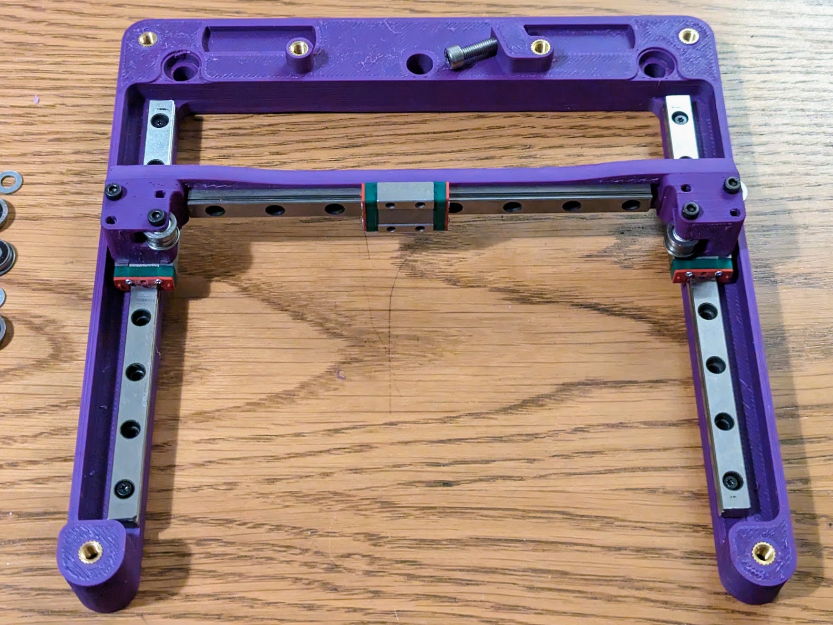
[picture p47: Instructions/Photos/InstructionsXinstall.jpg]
<p></a></p>

The Y rail screws can then be inserted and tightened one at a time working from the back forwards, each time you move forwards move the gantry as close to the screw as possible as this will ensure the rails get set parallel.

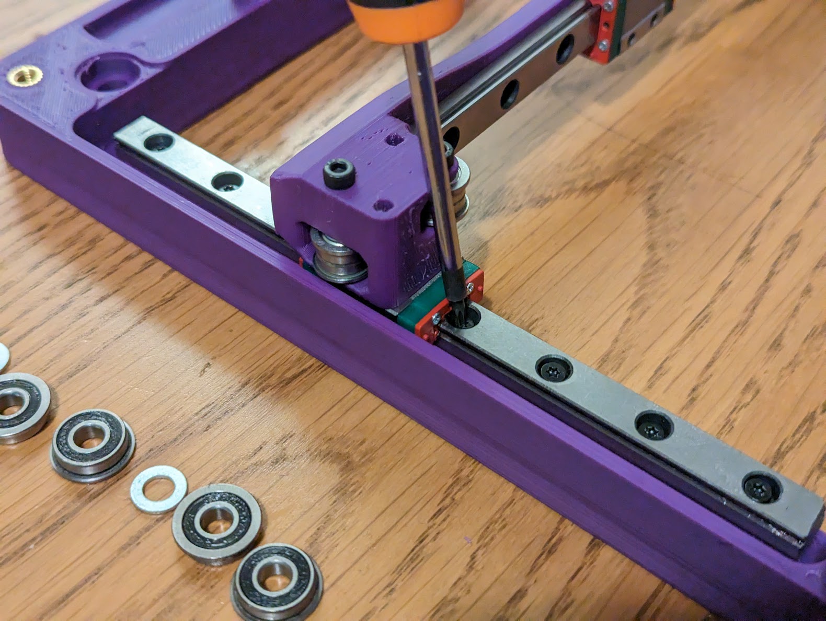
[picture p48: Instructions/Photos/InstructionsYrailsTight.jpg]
<p></a></p>

Once the Y rails are secured and parallel you can push the gantry all the way back, loosten the pulley screws again, insert the other ones in the gantry and re-tighten, this is just to ensure that the Y blocks are parallel to the rails.

At this point your gantry should smoothly move along the rails, if theres any points of binding then you might need to loosen the Y rails and try again.

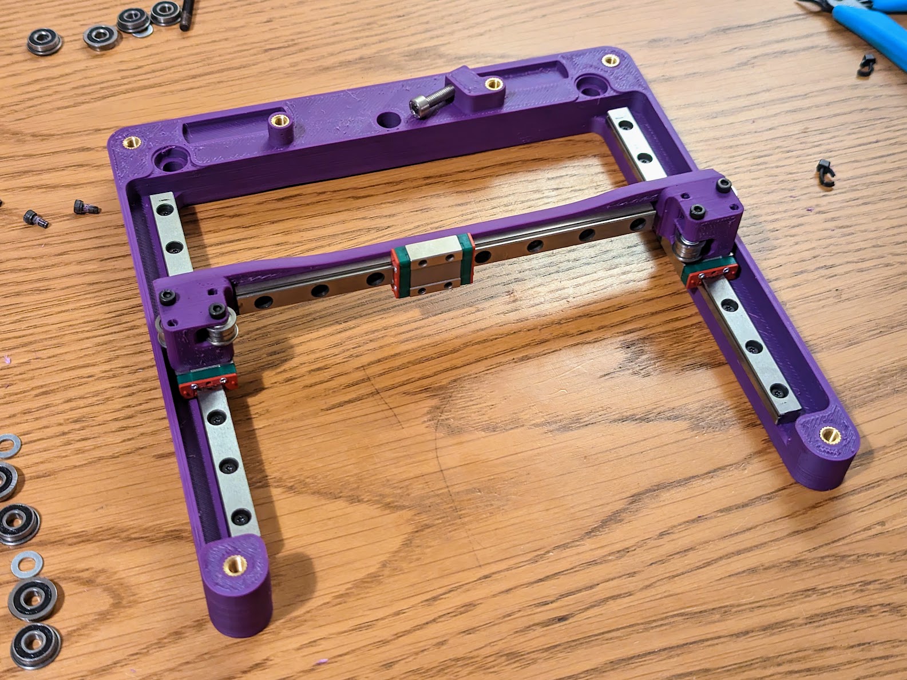
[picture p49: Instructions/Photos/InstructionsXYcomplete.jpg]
<p></a></p>

---

## Step 5 - Assemble The Belt Paths

The top part can be placed top side down with 6x M5x35 CSK screws in the 5mm holes.

2 of the 5mm ID bearings can be pushed into the bearing seats near the tensionsers

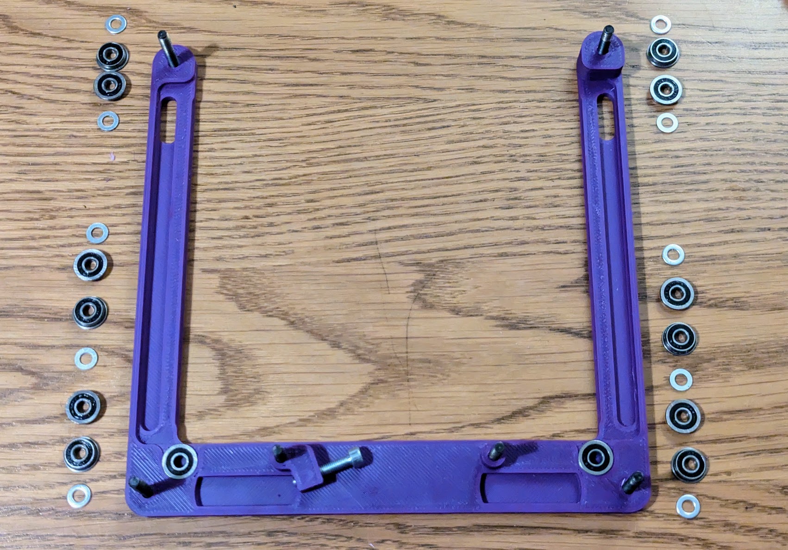
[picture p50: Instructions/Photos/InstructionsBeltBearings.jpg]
<p></a></p>

The bearing stacks can then be placed on top of these screws, the stacks on the arms go washer-bearing-bearing-washer. The stacks at the back are washer-bearing-bearing-washer-bearing-bearing-washer as shown above.

Once the stacks are complete they should look as shown below. The tensionsers can be placed in their slots with the sloped edges facing towards the center.

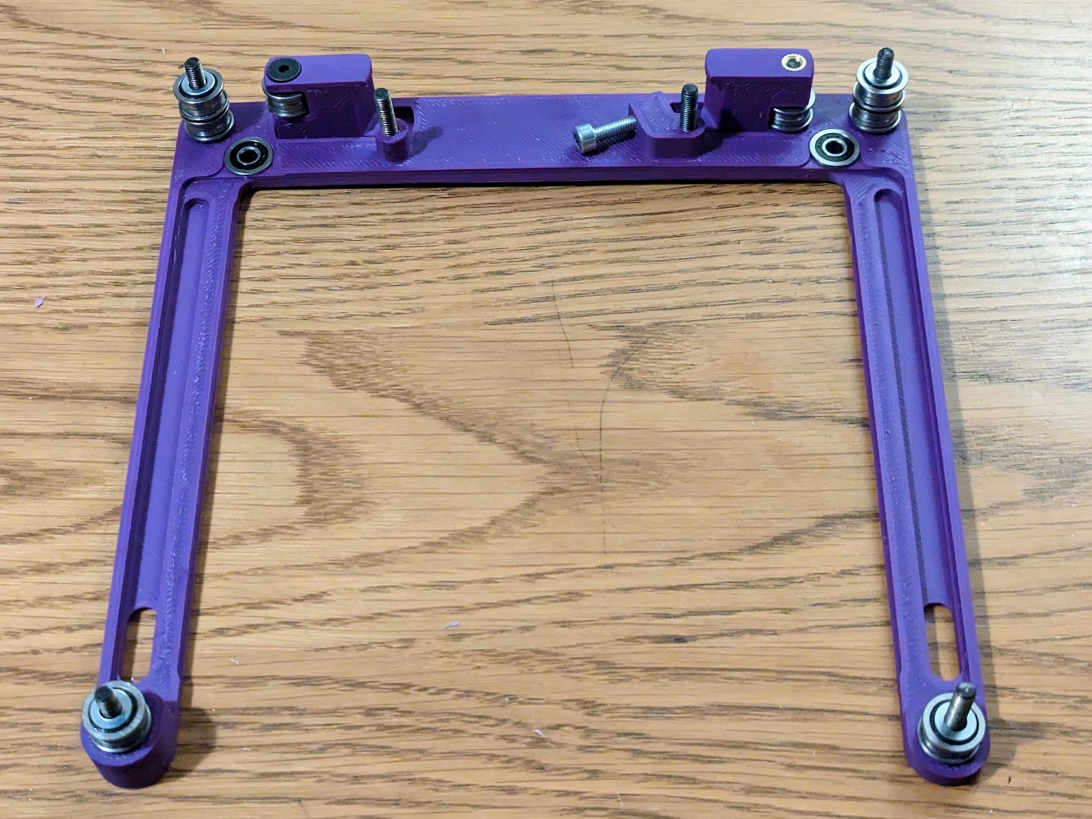
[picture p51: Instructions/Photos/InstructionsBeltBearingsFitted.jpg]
<p></a></p>

The XY stage mid section from earlier can then have the Drive Pulleys inserted into it, making sure the bearings seat firmly. I recommend to place them as shown below.

Note that i have also installed the M5x25 tensioning screws, it can be done later but its easier now.

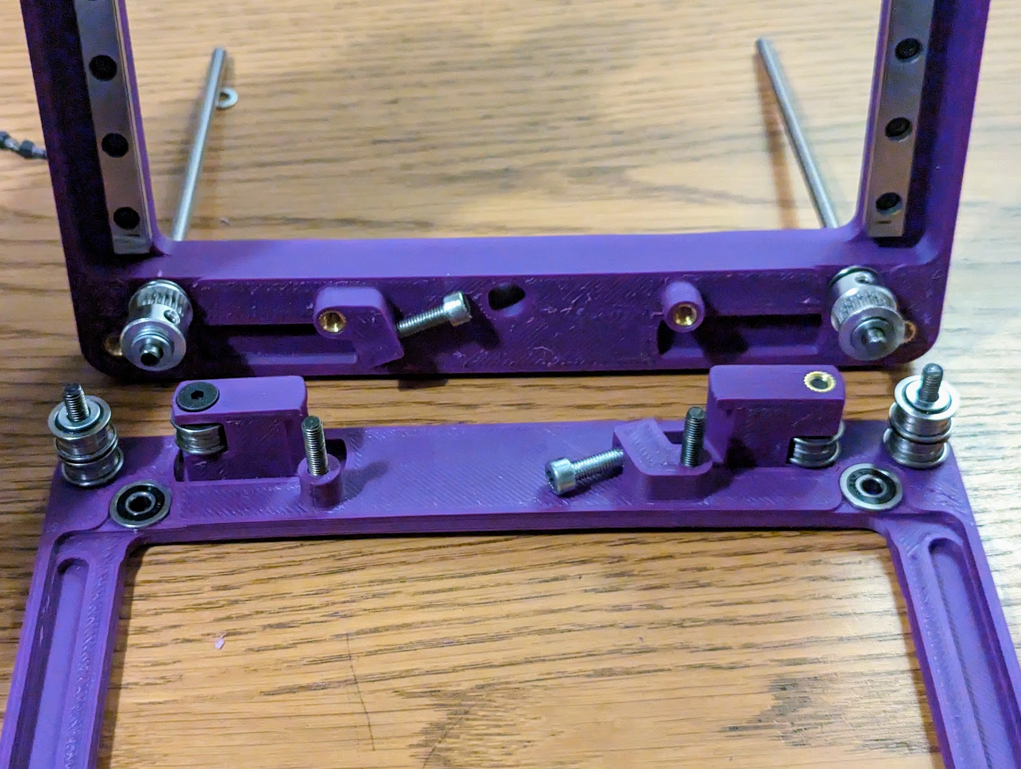
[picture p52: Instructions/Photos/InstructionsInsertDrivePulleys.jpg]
<p></a></p>

Now the Fiddly bit.

Both parts need to marry together, the best way i have found to do this is to carefully stand both parts together, making sure the screws don't fall out as you do it. 

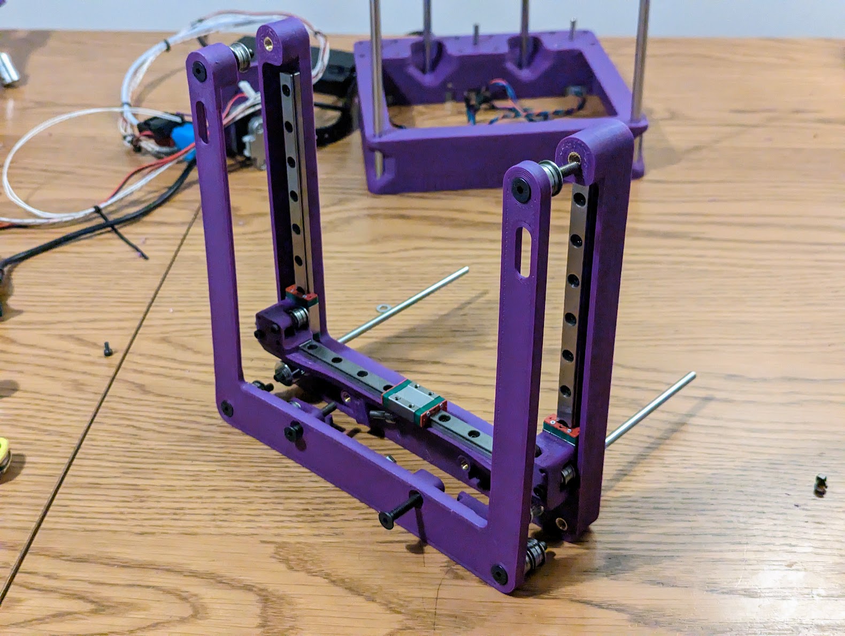
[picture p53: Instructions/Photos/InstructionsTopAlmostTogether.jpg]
<p></a></p>

Get them close enough that you can start the threads on the 4 bolts. Once all 4 are started you can push the 2 parts together ensuring that the tensioner blocks are correctly in their channels. then you can tighten down all 6 of the M5 CSK bolts.

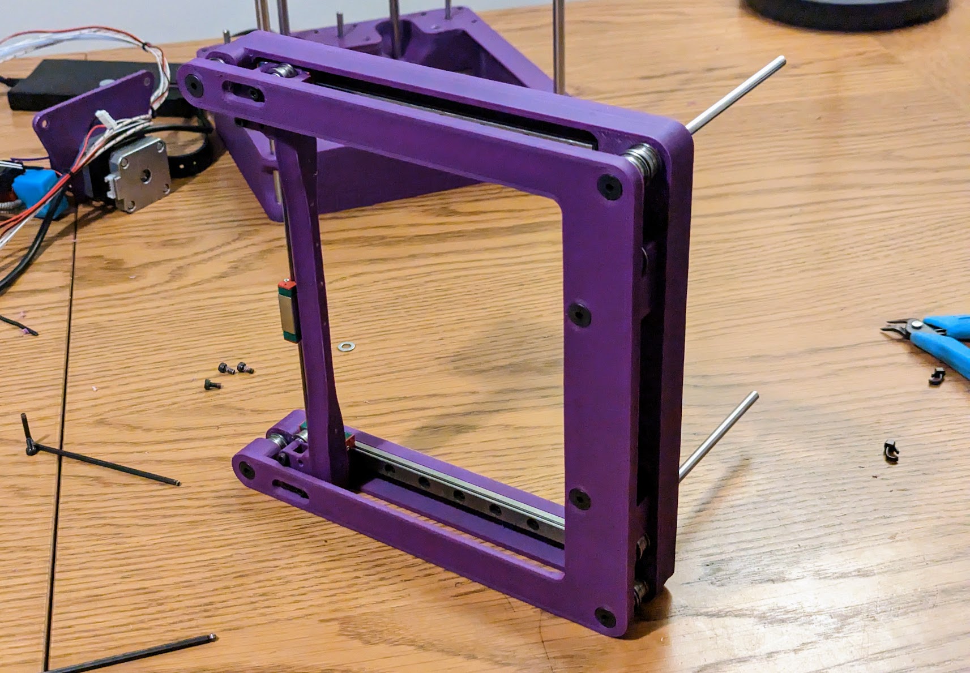
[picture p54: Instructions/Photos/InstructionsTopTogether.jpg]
<p></a></p>

---

## Step 6 - Put the top on the bottom

As the title says, put the top on the bottom. 

Be careful to ensure that all 4 8mm rods go into their holes correctly. Also make sure that the 5mm rods go into the couplers. if your print has any warp the rods might not line up up fully but just get them in there and the couplers and bearing stacks will ensure that everything aligns properly.

Make sure that the top is fully seated. Check this by measuring the distance from the base to the top, it should be the same at all 4 rods. 

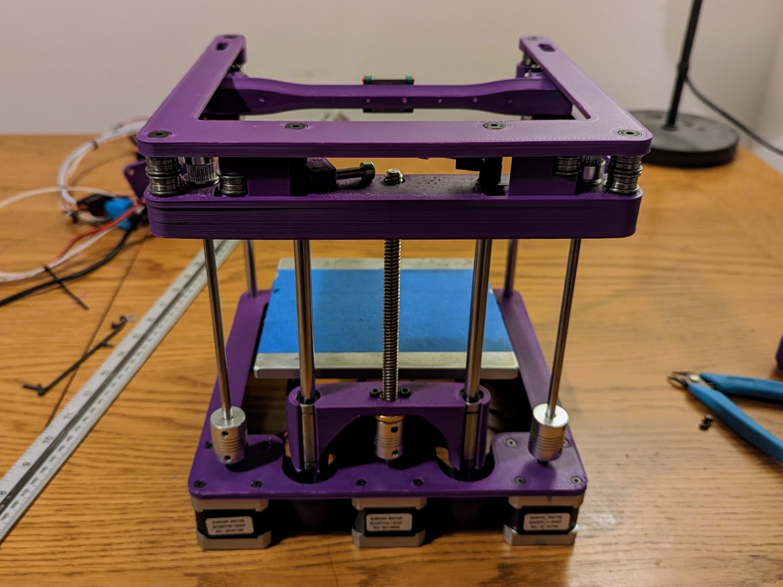
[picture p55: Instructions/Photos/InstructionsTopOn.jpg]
<p></a></p>

The couplers can now be tightened. there should be a gap between the stepper and the rod for the A/B motors which the coupler will cover.

For the Z the rod should rest directly on the stepper shaft to ensure reliable sensor-less homing. the coupler should be positioned so that the brass nut bottoms out on the coupler and leaves 1-2mm clearance between the bottom of the bed and the base as shown below.

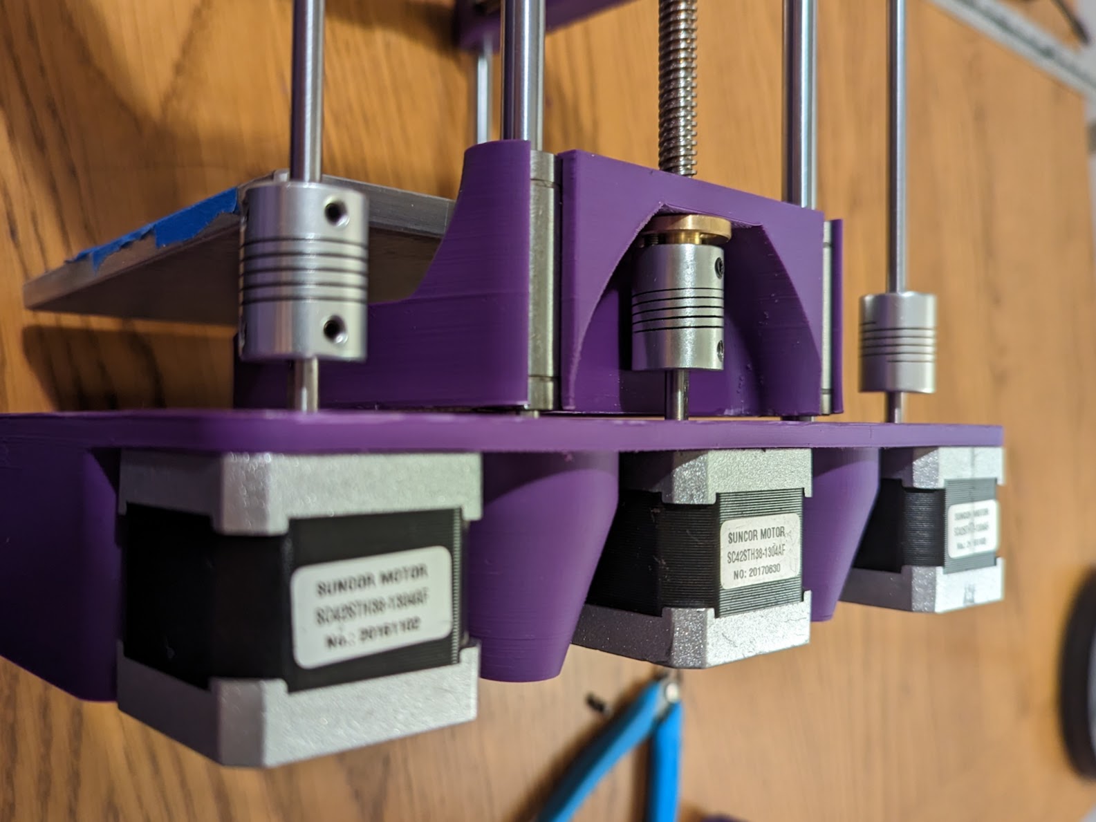
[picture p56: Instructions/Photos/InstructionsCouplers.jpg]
<p></a></p>

---

## Step 7 - Run the Belts

The belts get attached to the print head by inserting through the inner most hole from the back, then back through the outer hole, then cable tied so that some of the teeth lock together.

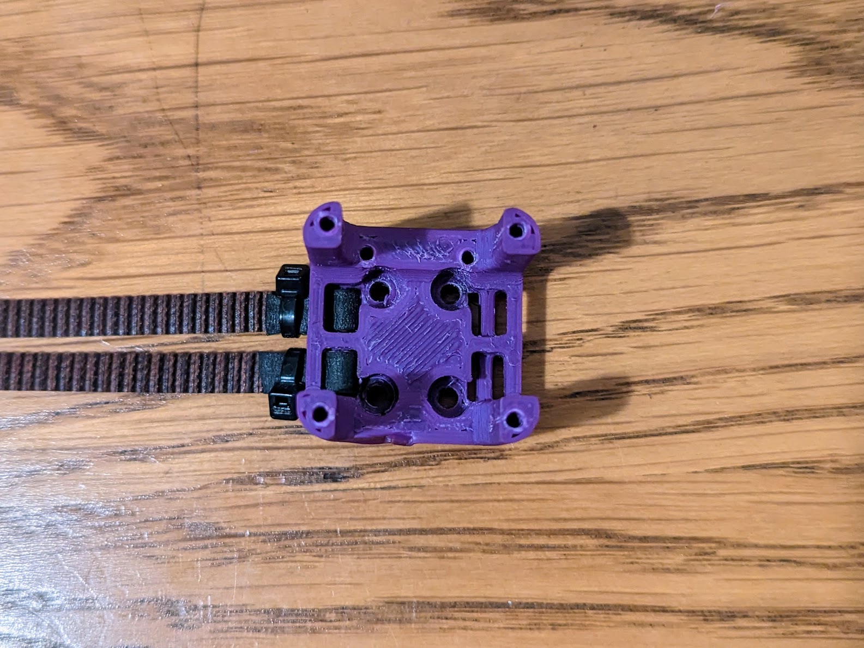
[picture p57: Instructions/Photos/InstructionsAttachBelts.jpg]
<p></a></p>

The print head can be held in place on the gantry by a single screw.

The lower belt passes all the way through the lower hole. the upper belt goes round the pulley in the gantry and then round the bearing at the front of the frame.

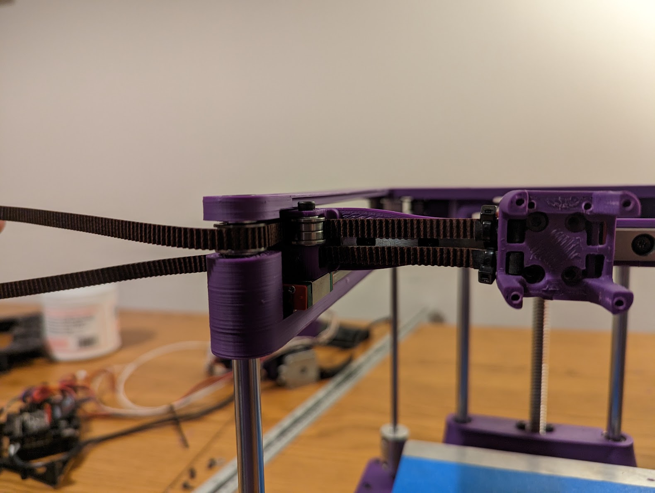
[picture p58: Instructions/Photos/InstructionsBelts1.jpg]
<p></a></p>

The lower belt passes all the way through the lower hole. the upper belt goes round the pulley in the gantry and then round the bearing at the front of the frame.

<p></a></p>

Belts are brought to the back corner. The upper belt goes all the way round the upper bearing, in round the pulley, then back out round the tensioner block. The lower belt just goes round the corner bearing.

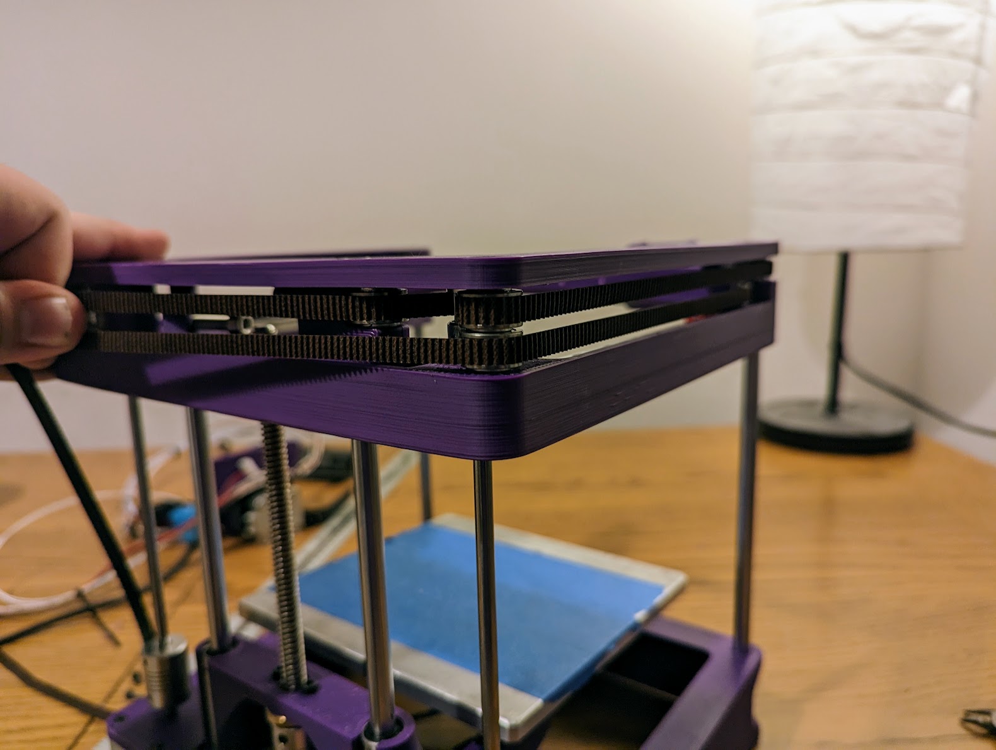
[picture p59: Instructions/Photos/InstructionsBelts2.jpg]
<p></a></p>

Now the other back corner, this time the lower belt goes round the tensioner, in round the pulley, out round the lower corner bearing. the upper belt just goes straight round the upper corner bearing.

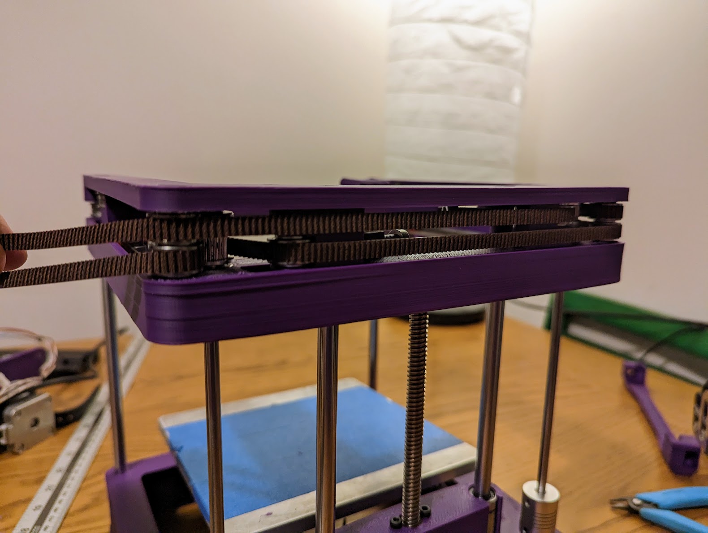
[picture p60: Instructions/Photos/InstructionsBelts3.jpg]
<p></a></p>

The upper belt now goes in to the gantry. The lower comes round the front corner bearing and back to the X gantry and round the lower gantry bearing.

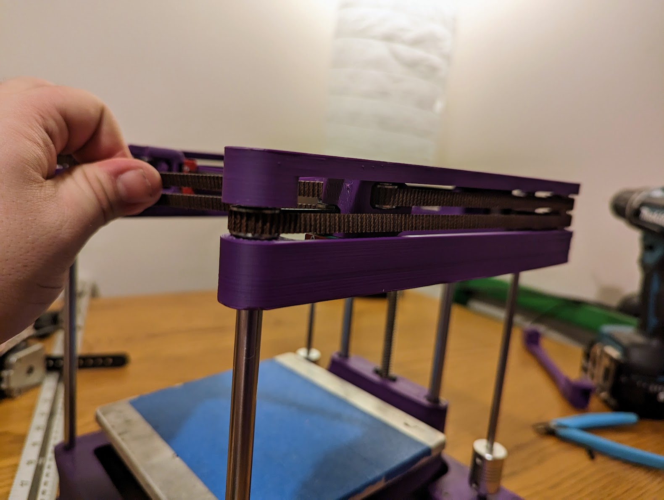
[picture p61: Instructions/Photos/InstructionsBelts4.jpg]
<p></a></p>

Take the screw holding the tool head out and then both belts then get inserted into the inner holes of the print head

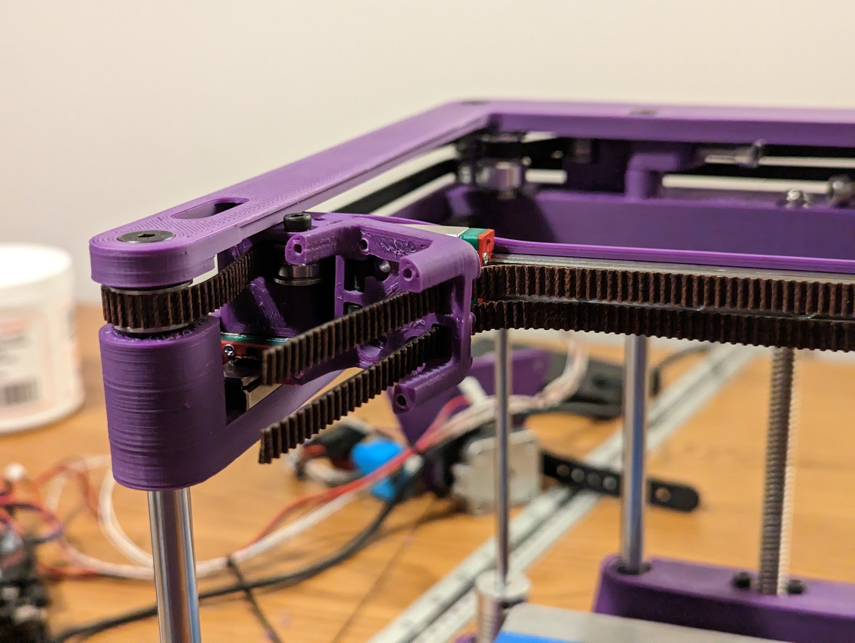
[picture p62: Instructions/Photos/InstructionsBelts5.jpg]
<p></a></p>

Then back through the outer hole. 

At this pint pulling the ends will cause the belts to tighten. Pull them to a good level of tight by hand. Work your way round ensuring that the belts are sat correctly in the pulleys all the way round. belts should be reasonably tight.

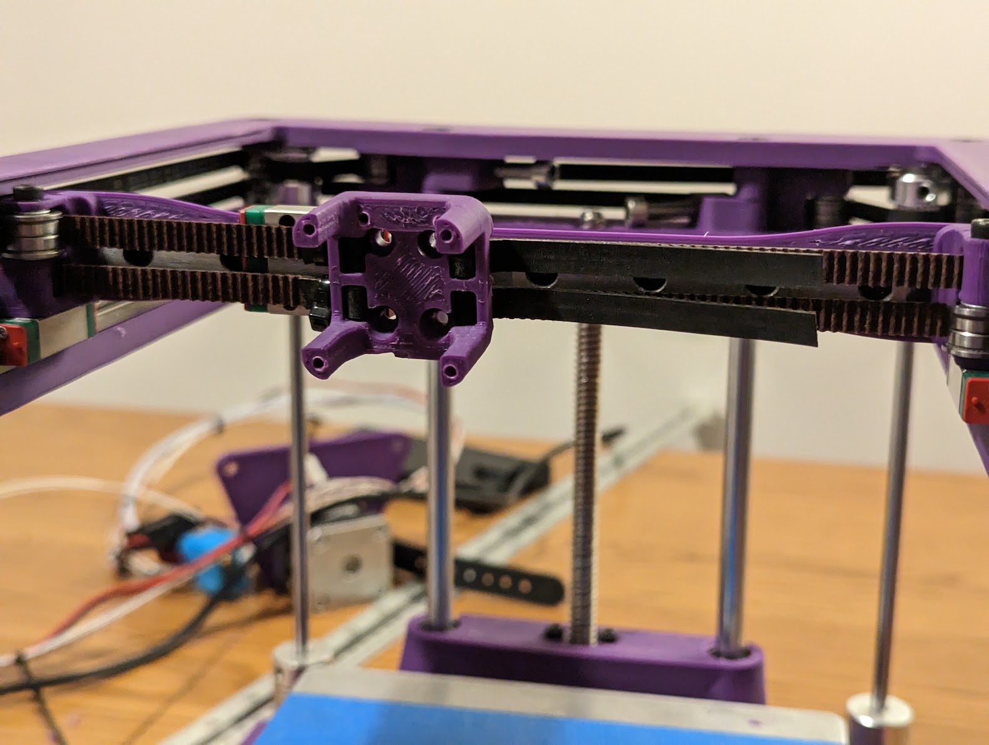
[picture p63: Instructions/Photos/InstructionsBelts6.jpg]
<p></a></p>

You can now secure the print head to the X bearing block and cable tie the other end of the belts to finaly secure them. 

Now is your chance to do a better job of cutting the belts to length that i did.

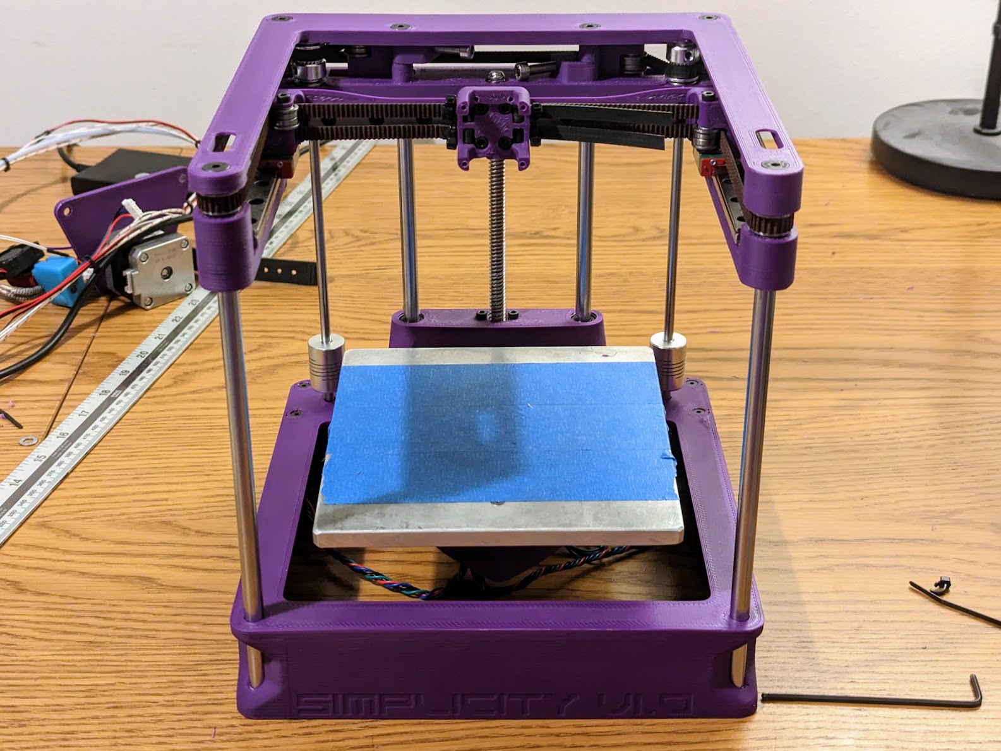
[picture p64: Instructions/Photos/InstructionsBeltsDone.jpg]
<p></a></p>

If you want to test things rotating the couplers by hand should move to print head smoothly.

---

## Step 8 - Assemble Hot End

Home stretch now, my instruction from here doesn't really cover to much detail over wiring and cable routing as i feel like plenty of other guides cover this.

Hot end heatsink block screws in with 2x M2.5x16 self tapping screws

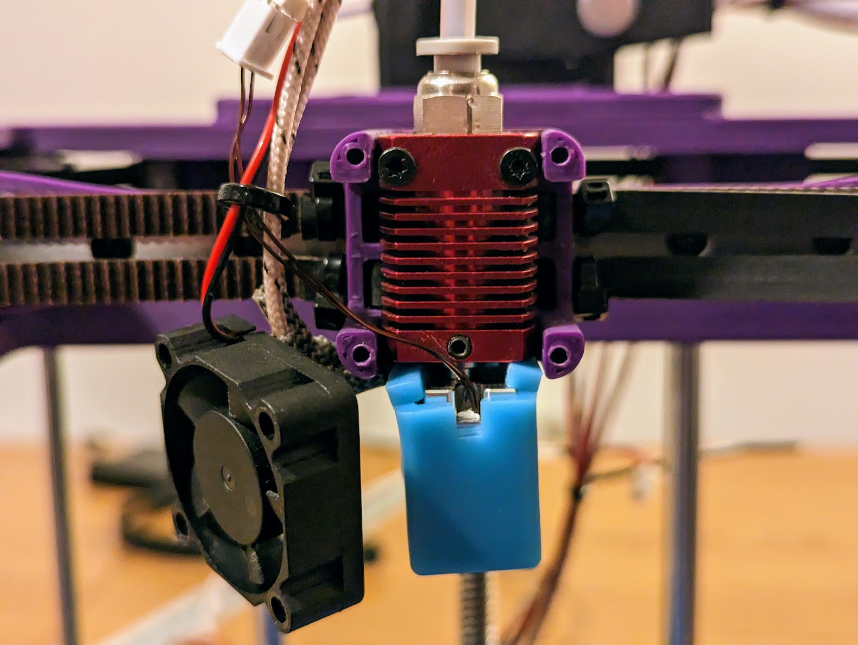
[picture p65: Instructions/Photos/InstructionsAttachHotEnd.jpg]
<p></a></p>

3010 fan then screws on the front with another 4 self tapping screws.

I found it useful to secure the wires with a cable tie that can be placed around the top fan support.

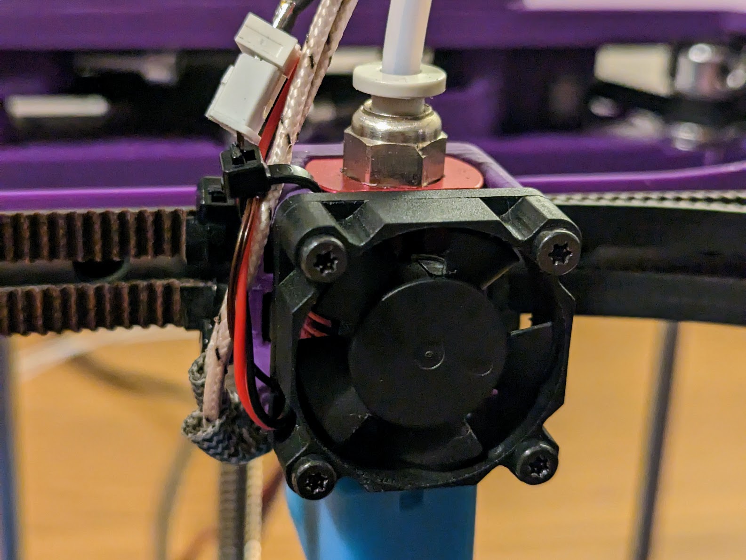
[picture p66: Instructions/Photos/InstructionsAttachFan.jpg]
<p></a></p>

Extruder mount plate (if your using mine) is screwed in between the extruder and its stepper motor.

This can the be mounted to the printer by removing the 2 middle rear M5x35 screws, placing the mount on top and replacing the screws 

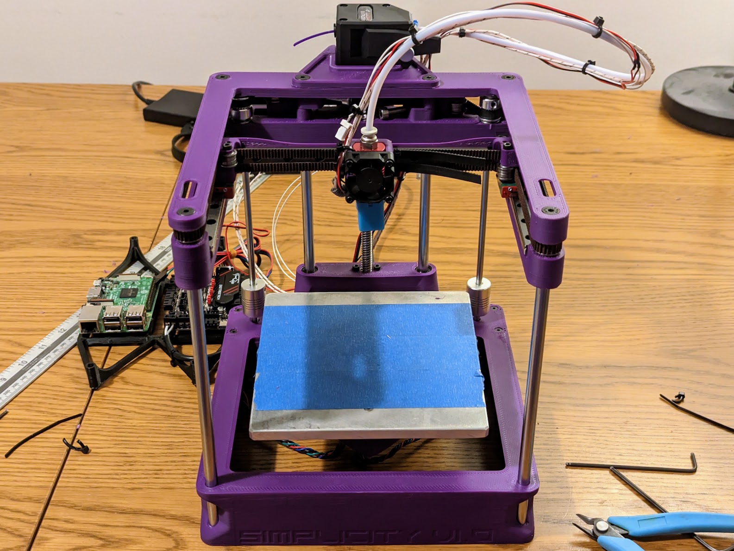
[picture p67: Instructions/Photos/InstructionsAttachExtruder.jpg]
<p></a></p>

---

## Step 9 - Install Electronics

Raspberry pi and SKR Pico can be mounted to the electronics tray with some of the small self tapping screws.

Power can be wired in from external PSU and cable tied for strain relief.

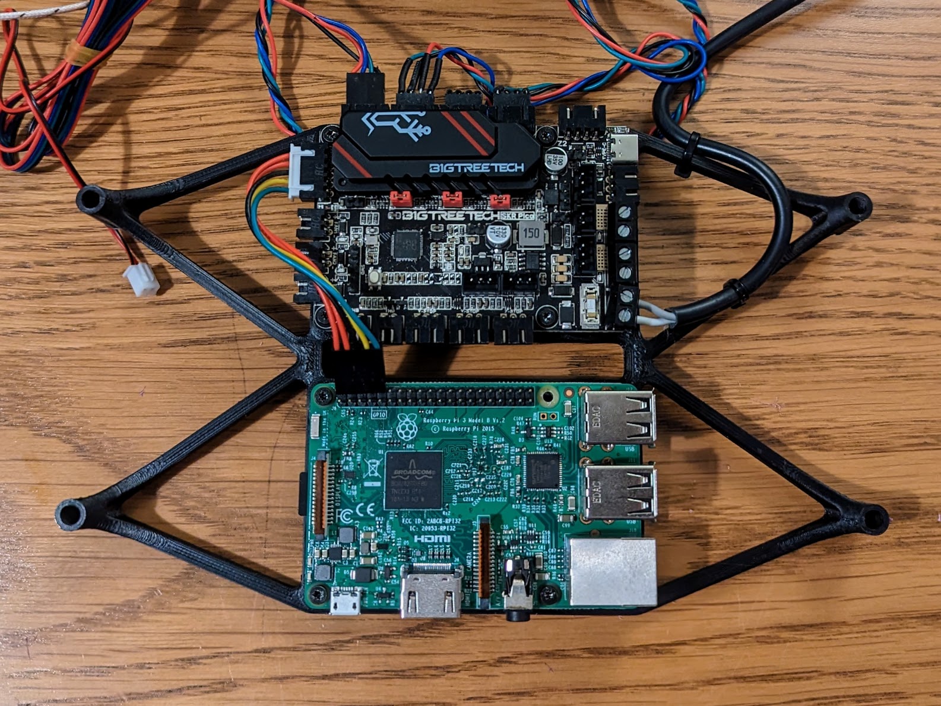
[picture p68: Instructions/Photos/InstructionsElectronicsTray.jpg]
<p></a></p>

If your using an electronics tray, There are additional places in the base where Heat Set Inserts can be added for securing accessories. My tray just uses the other most holes on the sides. But these can be fitted as and when they are needed.

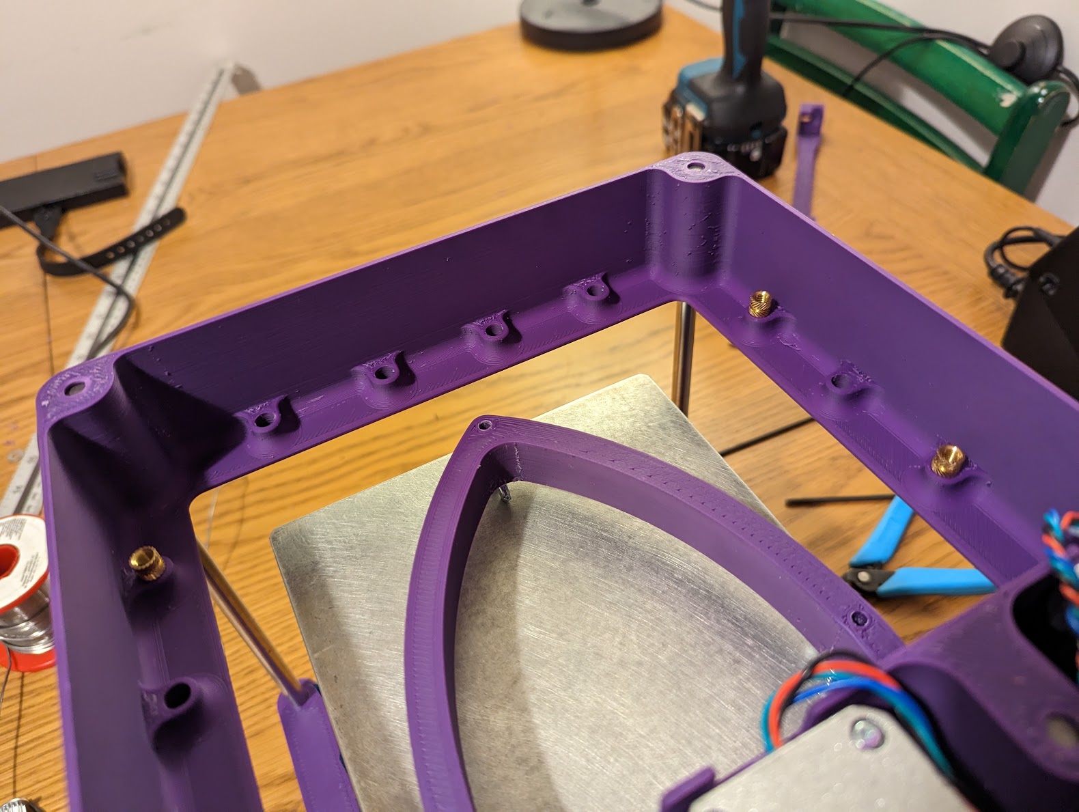
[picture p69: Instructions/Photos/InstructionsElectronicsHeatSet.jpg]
<p></a></p>

Electronics tray can then be installed.

Steppers plug in, Hot End gets wired in, thermistor plugs in, hot end fan plugs in.

Jumpers for A, B and Z added to pico for sensor-less homing.

<p></a></p>

All cables that come out he the electronics area can pass through this small cut out.

Theres a small hole below it allowing the cables to be secured into the gap with a cable tie.
<p></a></p>

---

## Step 10 - Done

Flip it back over and marvel at what you have built.

<p></a></p>

Well done. 

Now you just need to follow a tutorial to install and set up klipper and your ready to print.

TODO (for me):
Add a link to my example klipper config files and homing scripts.

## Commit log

2023-02-12 Initial commit with parts used for my build
    [SimplicityBase.3mf, SimplicityBed.3mf, SimplicityElectronics.3mf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]
2023-02-12 CAD directory now has README
2023-02-12 changed some file directories
    [SimplicityBase.3mf, SimplicityBed.3mf, SimplicityElectronics.3mf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]
2023-02-15 recess screw chamfer a little to improve printing
    [SimplicityBase.3mf]
2023-02-15 Added STEP file to CAD
